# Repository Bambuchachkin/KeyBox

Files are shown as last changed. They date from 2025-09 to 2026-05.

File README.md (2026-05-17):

# KeyBox 🔑

(*Для того чтобы принять участие в обсуждении проекта можете перейти по ссылке https://github.com/Bambuchachkin/KeyBox/discussions/1)

## Цель проекта 🎯
Создать устройство, предназначенное для одновременного хранения ~ 10 ключей от
аудиторий в корпусах МФТИ. Оснастить его системой автоматического контроля
доступа к ключам через карты-пропуска. Вести учёт пользователей и времени, которое
ключи были у них на руках.

## Итоги работы ✨

### По итогам работы нашей команде удалось выполнить все поставленные цели:
1. ✅ Создано устройство для хранения 10 ключей
2. ✅ Установлен замок для ограничения доступа к ключам
3. ✅ Инсталирована светодиодная лента для улучшения пользовательского опыта
4. ✅ Реализована работа с картами-пропусками
5. ✅ Спроектирована база данных пользователей
6. ✅ Налажена работа с таблицами формата .xlsx для удобства работы с устройством
7. ✅ Разработаны методы работы с устройством с помощью консоли
8. ✅ Разработано и произведено функциональное устройство

<p align="center">
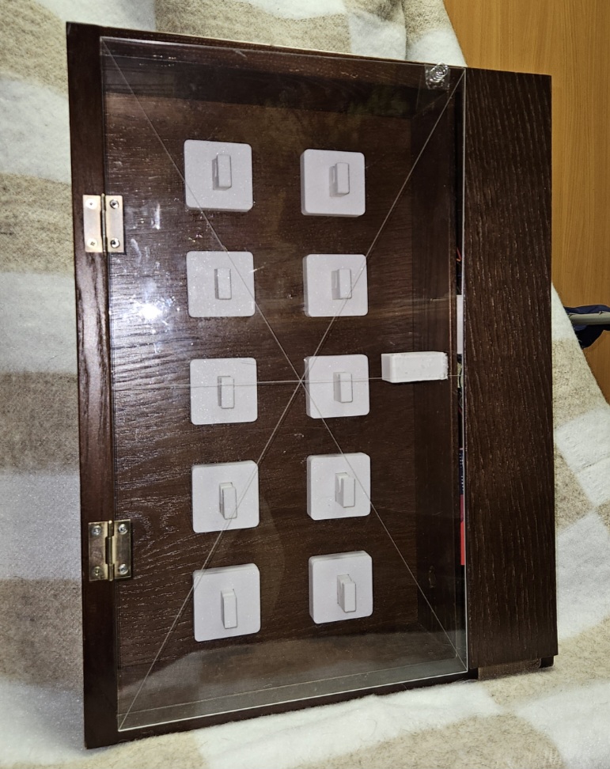
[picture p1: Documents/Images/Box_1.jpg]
  
</p>
<p align="center">
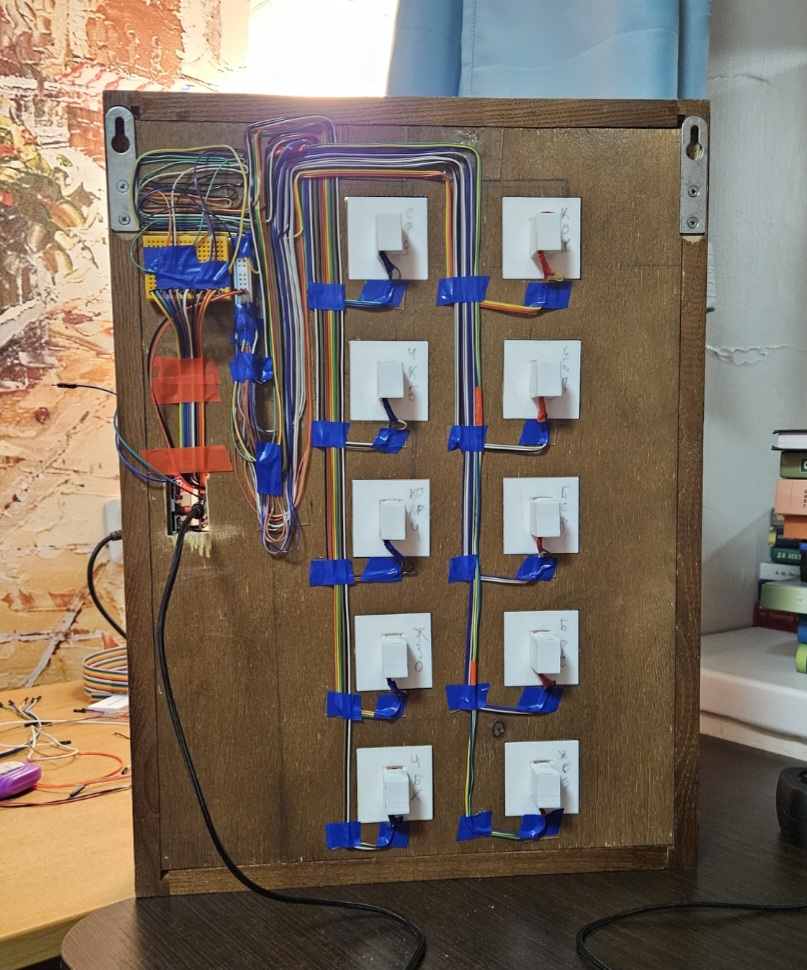
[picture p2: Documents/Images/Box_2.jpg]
  
</p>

### Решенные проблемы: 🔧
В процессе работы возникали проблемы различного уровня сложности. Среди наиболее острых, но разрешенных оказались:
1. Механизм открытия и закрытия двери, требующий от пользователя минимум действий, а именно приложить карту-пропуск и захлопнуть дверцу после взятия/возвращения ключа. Механизм был реализован при помощи системы: сервопривод, штифты и клинья, возвратные пружины.
2. Реализация наиболее удобных способов взаимодействия персонала с устройством. Такими являются консольное взаимодействие для быстрой регистрации и редактирования профилей пользователей и exel-таблицы для обработки базы данных и журнальных записей (приходы, уходы, взятые ключи).

### Возможное развитие проекта: 🚀
Полученное изделие имеет массу возможностей для улучшения:
1. Дистанционное взаимодействие посредством сети wi-fi
2. Оповещающие устройства (сигнальный динамик, информирующий дисплей)
3. Система автономного реагирования (автоматические ограничения для недобросовестных пользователей)

## Далее вы можете более подробно ознакомиться с историей развития проекта 📖

### Принципиальная схема цепи и взаимодействия ее компонент:

<p align="center">
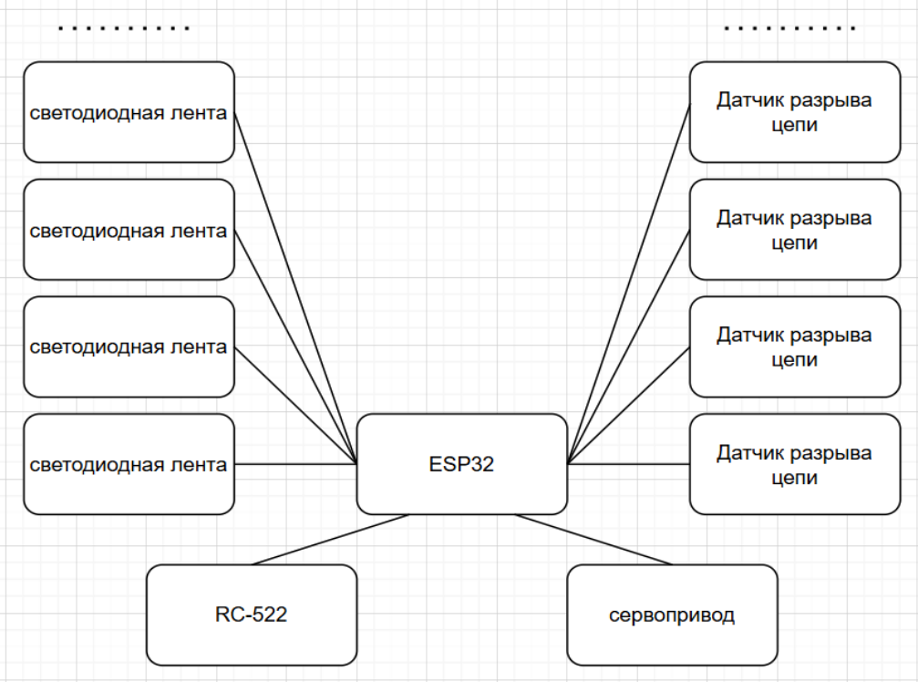
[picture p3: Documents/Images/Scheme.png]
  
</p>
<p align="center">
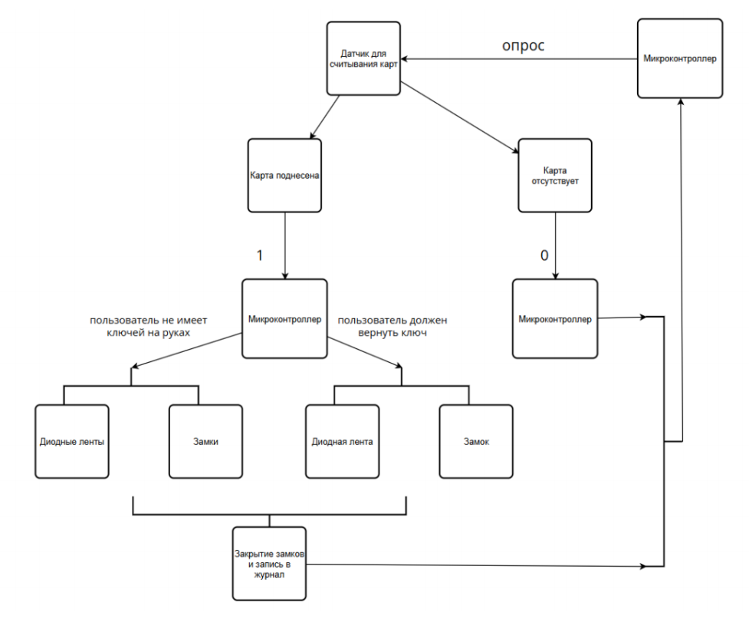
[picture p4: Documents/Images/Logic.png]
  
</p>

## Ход работы

### Особенности физтеховских карт-пропусков:
<table>
<tr>
<td style="border: none;">

Наименование: mifare classic 1k

Рабочая частота: 13.56 МГц

Требует аутентификации: Для данных, но не для UID

</td> </tr> </table>

### Взаимодействие с картой:
Общение с картами будет осуществлятся при помощи считывателя RC522.
<p align="center">
  ESP32 Tetris Console
</p>
<p align="center">
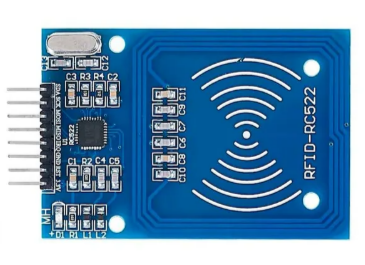
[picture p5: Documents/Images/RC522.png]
  
</p>
<!-- ![Отрисовка карты.](Documents/Images/RC522.png) -->

### Работа в материале

Схема работы детектирующего устройства:
<p align="center">
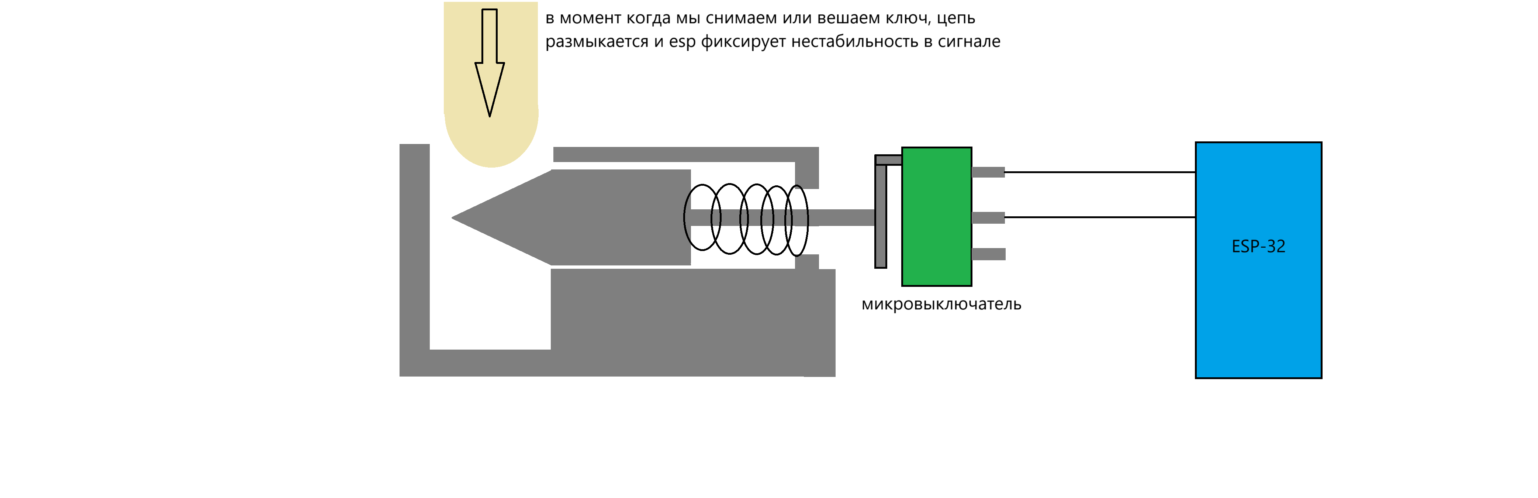
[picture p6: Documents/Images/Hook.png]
  
</p>

Модель корпуса ключницы:
<p align="center">
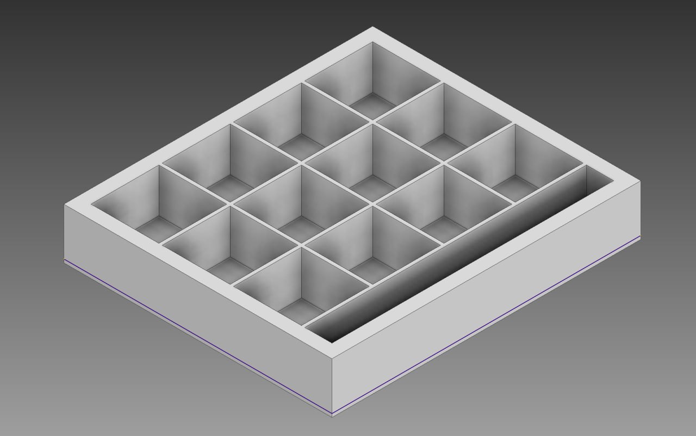
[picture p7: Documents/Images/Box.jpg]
  
</p>

Сделан корпус из дерева (дополнительные отверстия будут делаться на физтех-фабрике)
<p align="center">
  ESP32 Tetris Console
</p>
<!-- <img width="767" height="1207" alt="image" src="https://github.com/user-attachments/assets/810f8d19-dff7-42e2-9041-3b519ff64c55" /> -->
<!-- 
Реализация чтения данных пользователей из таблицы (предитоговая версия):
![Отрисовка карты.](Documents/Images/json_read.png) -->

### Написание кода
Реализация взаимодействия с RC522:
<p align="center">
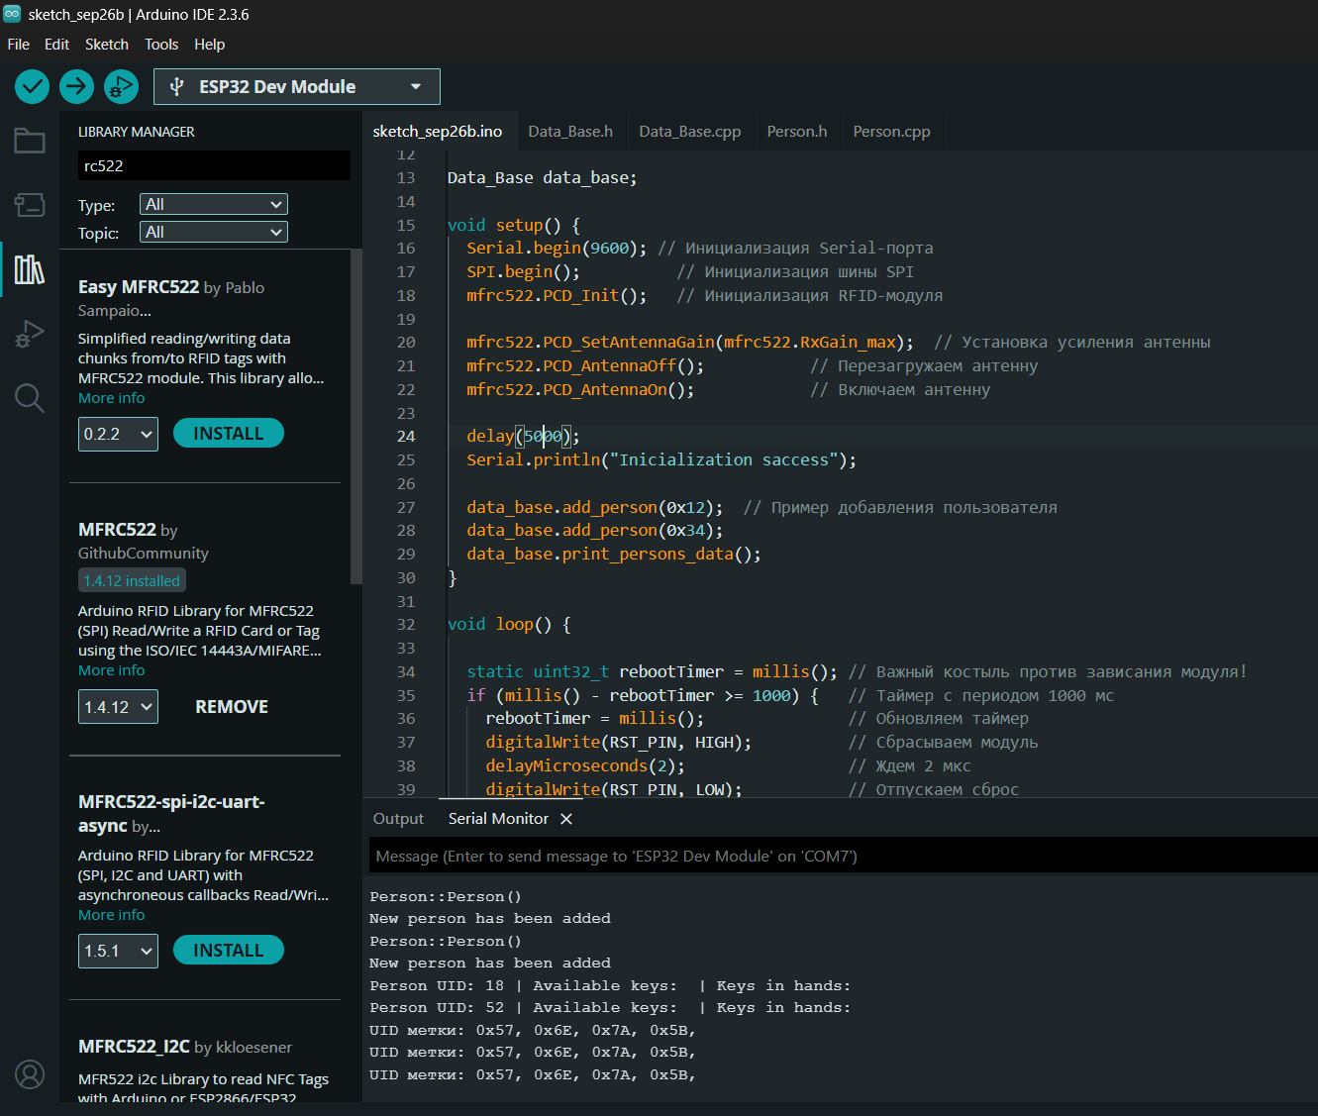
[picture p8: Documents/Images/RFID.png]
  
</p>

Реализация обработки команд с консоли:
<p align="center">
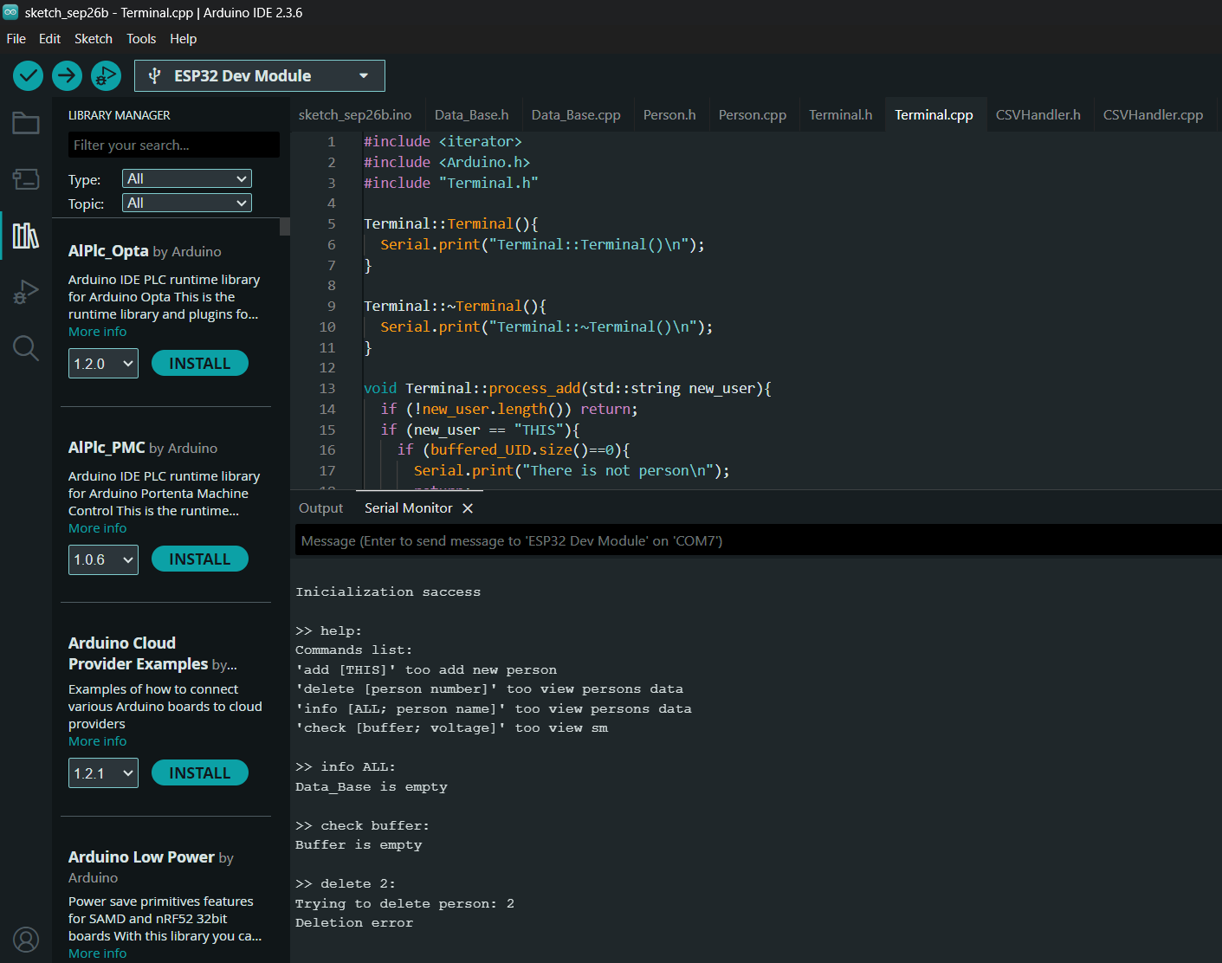
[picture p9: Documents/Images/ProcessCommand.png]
  
</p>

Реализация работы с пользователями:
<p align="center">
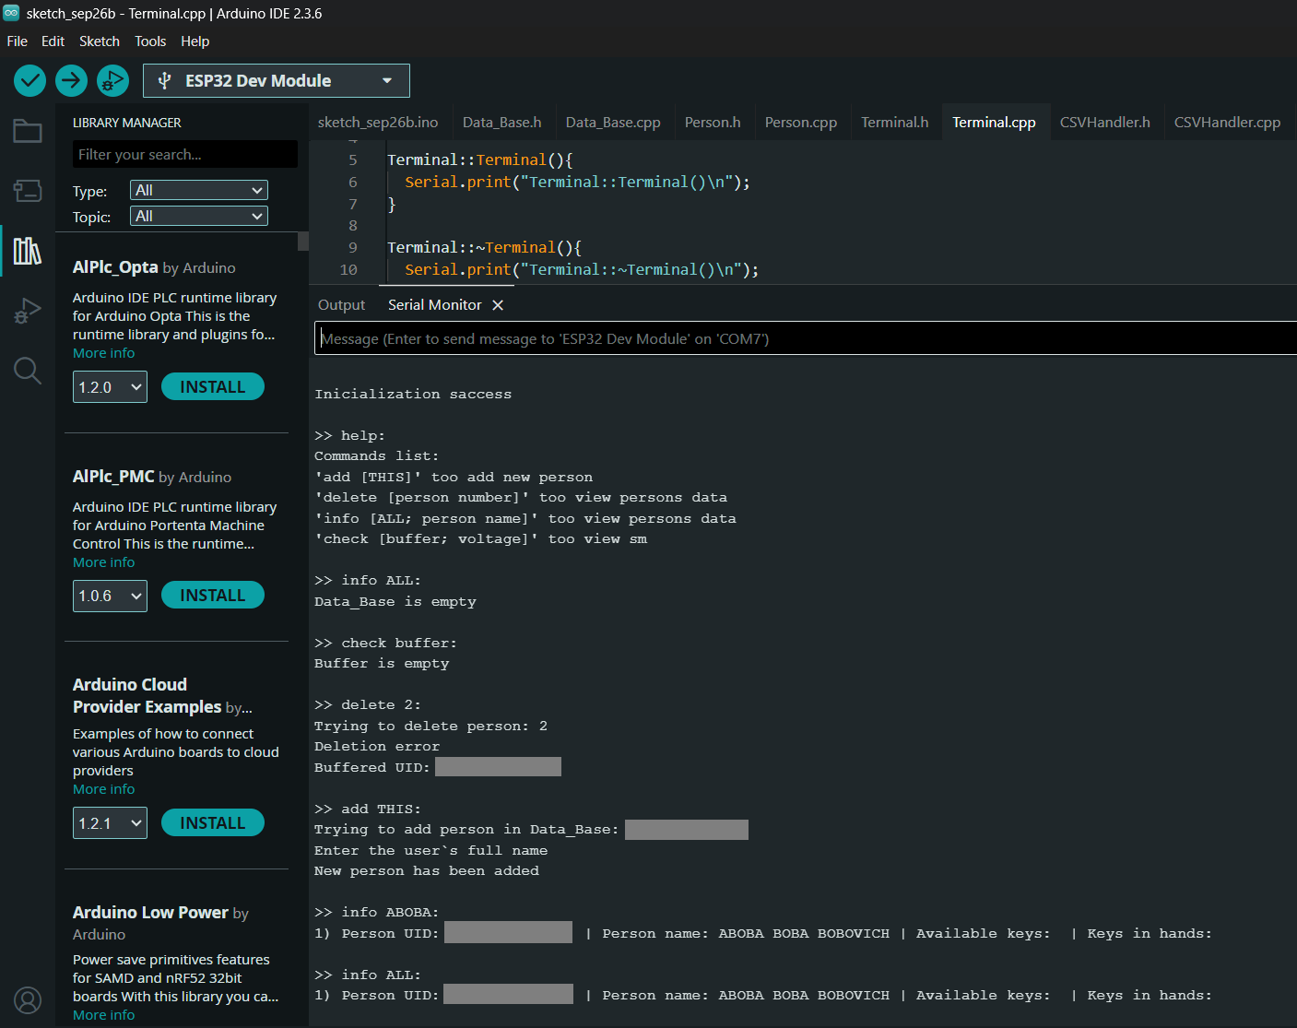
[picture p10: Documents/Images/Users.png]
  
</p>

Разработка структуры хранения данных:
<p align="center">
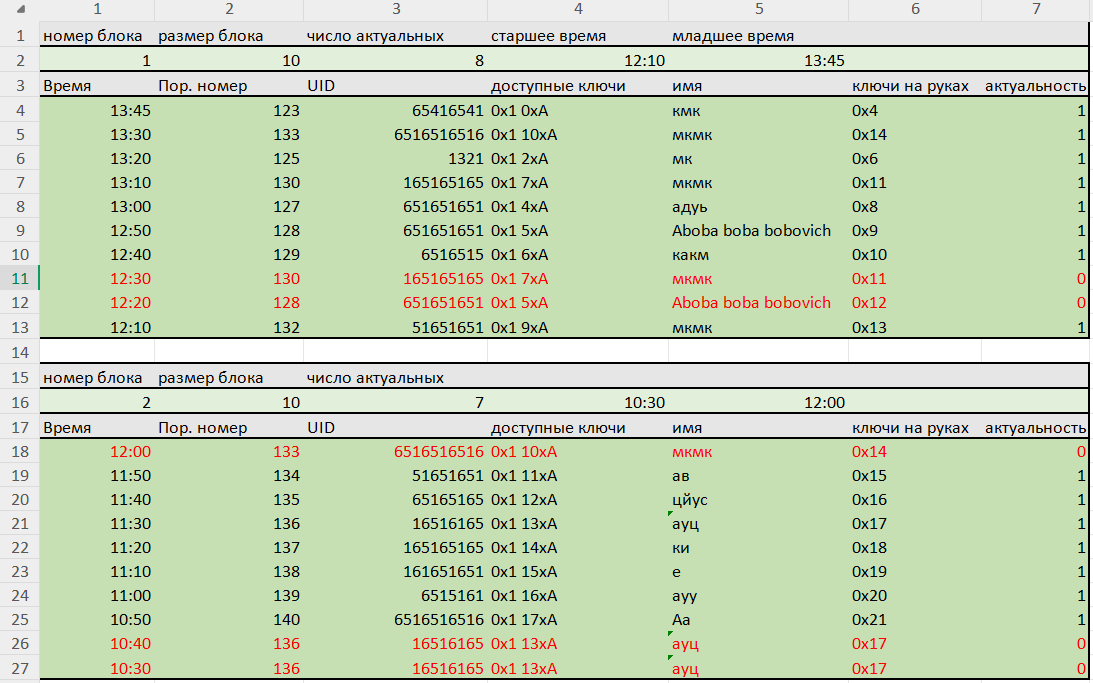
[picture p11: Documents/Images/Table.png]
  
</p>

Реализация чтения и записи данных в таблицу (тестовые отправки):
<p align="center">
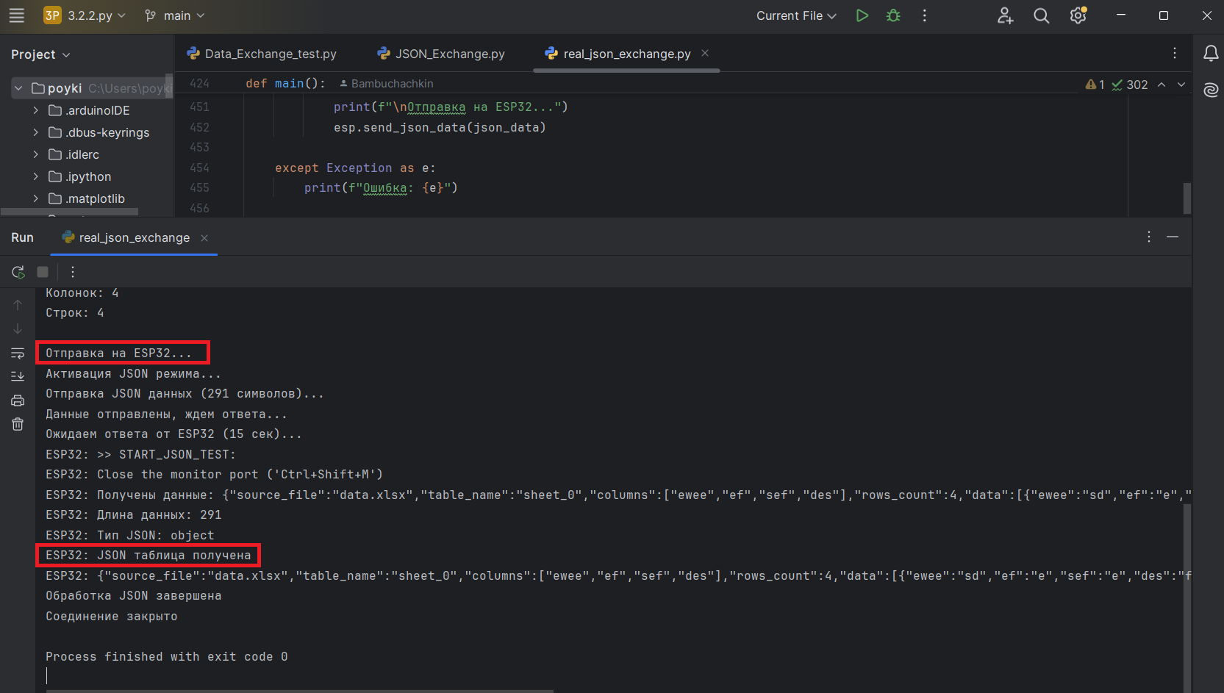
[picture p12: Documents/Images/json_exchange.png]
  
</p>

Реализация хранения и восстановления данных из постоянной памяти:
<p align="center">
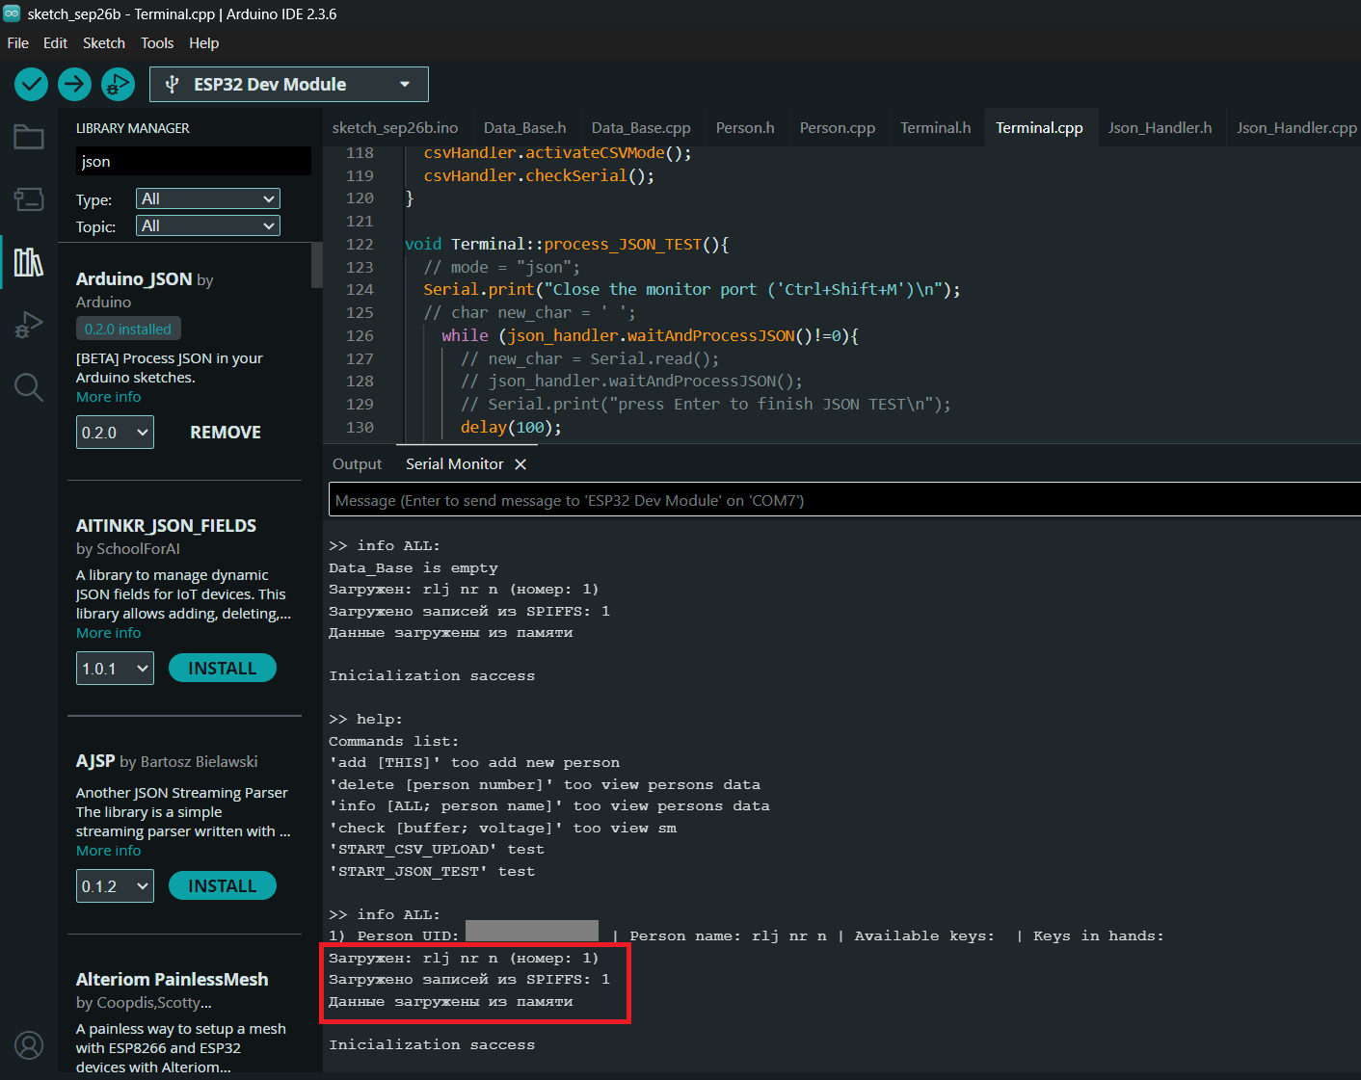
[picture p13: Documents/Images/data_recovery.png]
  
</p>

<!-- Добавлен кармашек для  зажима микропереключателя:
<img width="1541" height="1035" alt="image" src="https://github.com/user-attachments/assets/2c278192-2b9a-40d1-a9de-ddc6e570d0b0" />

Доработана основная платформа для закрепления кармашка в ней, так же увеличен радиус отерстия для пружинки:
<img width="1212" height="1104" alt="image" src="https://github.com/user-attachments/assets/5a2353b9-1f5b-4b1b-9aa3-503ce4ea96b2" /> -->

Окончательная реализация чтения данных пользователей из таблицы:
<p align="center">
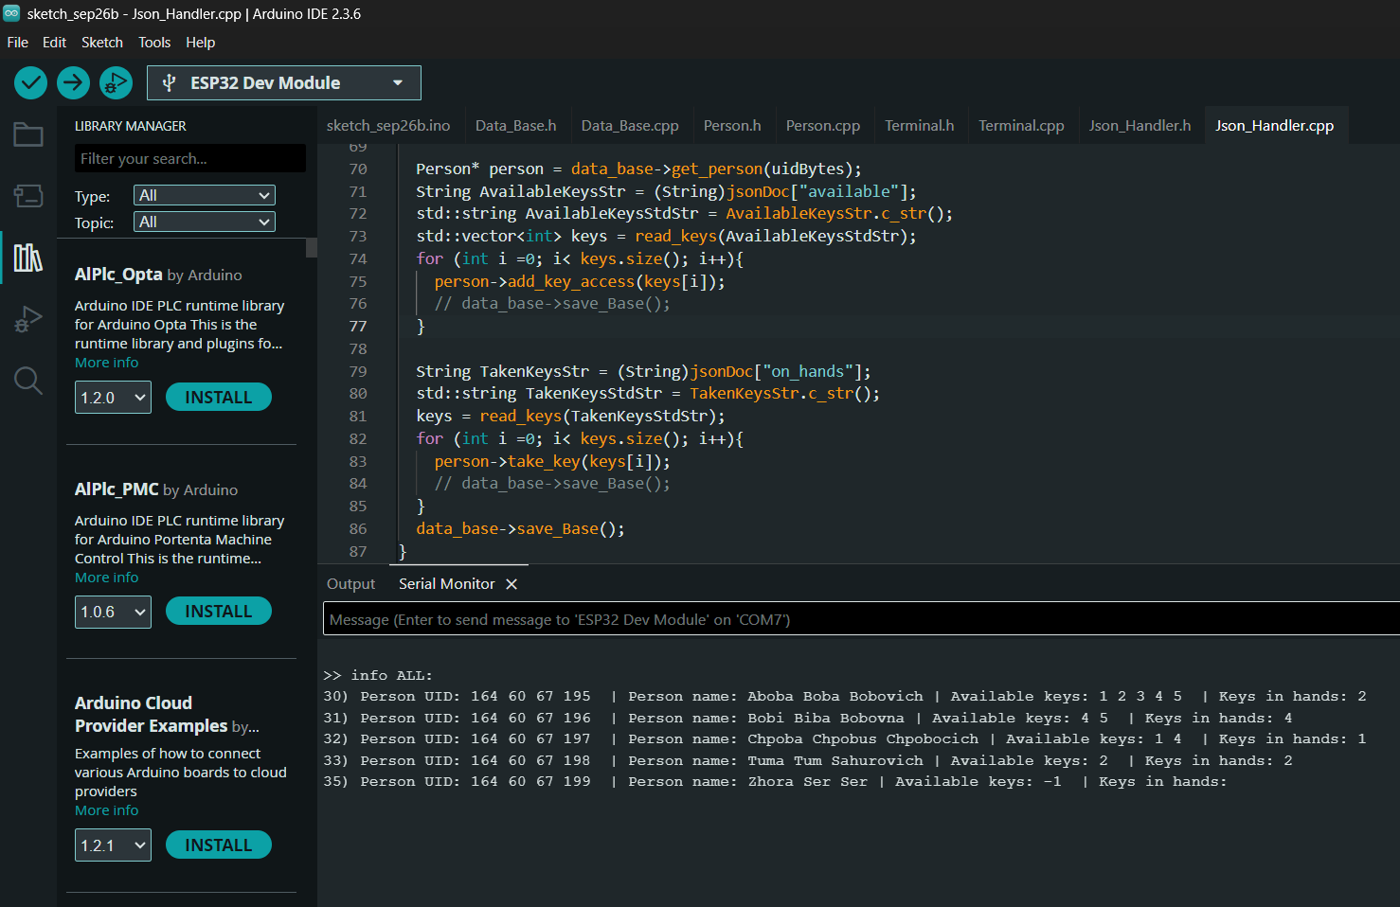
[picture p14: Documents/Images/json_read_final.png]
  
</p>

Сборка и тестирование 2ух узлов схемы + отладка кода:
<p align="center">
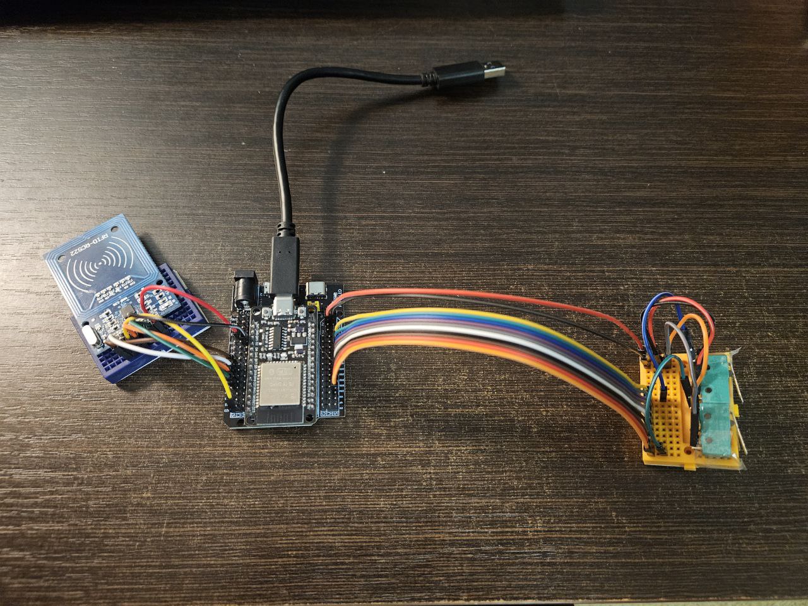
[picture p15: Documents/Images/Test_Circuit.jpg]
  
</p>

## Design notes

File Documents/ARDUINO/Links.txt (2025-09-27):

https://github.com/ljos/MFRC522/blob/master/MFRC522.h

https://alexgyver.ru/arduino-rfid/

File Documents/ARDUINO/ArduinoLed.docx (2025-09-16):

Основа всего проекта – это Arduino. Будем использовать Arduino Uno R3.

Необходимые о ней данные:

Характеристики Arduino UNO R3:

- Напряжение питания: 5 В
- Входное напряжение (рекомендуемое): 7-12 В
- Входное напряжение (предельное): 6-20 В
- Цифровой ввод-вывод: 14 линий (6 из них - ШИМ)
- Аналоговые входы: 6
- Постоянный ток на линиях ввода-вывода: 40 мА
- Постоянный ток на линии 3.3В: 50 мА
- Flash-память: 32 кб, 0.5 кб из них используются для загрузчика
- SRAM-память: 2 кб
- EEPROM-память: 1 кб
- Тактовая частота: 16 МГц

Для работы с подсветкой подойдет к примеру такая лента:

# https://giant4.ru/catalog/spi-lenta/ws2812b-60-ip33/? WS2812B 60 led

Или такая: https://www.ozon.ru/product/adresnaya-lenta-ws2812b-60-led-ip67-2-m-2210055581/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 (https://www.ozon.ru/product/adresnaya-lenta-ws2812b-60-led-ip67-2-m-2210055581/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) (идентичная)

Теперь по подключению:
1. Ограничение по Arduino Uno:

- Arduino Uno управляет лентой только по одному цифровому пину.
- Управление можно вести хоть 1000 светодиодов — ограничение в оперативной памяти (2 КБ).
- На каждый диод нужно 3 байта (RGB). 2000 байт ÷ 3, получается где-то около 600 светодиодов максимум.
- В этом случае дофига короче выйдет

Питание: ограничение только блоком питания. (Все зависит от него!!!!) От самой ардуинки лучше не питать более 10 диодов.

https://xn--18-6kcdusowgbt1a4b.xn--p1ai/ws2812b-%D0%B0%D1%80%D0%B4%D1%83%D0%B8%D0%BD%D0%BE/ (https://xn--18-6kcdusowgbt1a4b.xn--p1ai/ws2812b-%D0%B0%D1%80%D0%B4%D1%83%D0%B8%D0%BD%D0%BE/) - здесь хорошо описано подключение нашей ленты (если надо выведу информацию в README)

+5В блока питания ---- +5В ленты

GND блока питания ---- GND ленты

+--- GND Arduino

DIN ленты ----------- Цифровой пин Arduino (например, D6 через резистор 330 Ом) – это в слусае наличия блока питания ( повербанк)

Под конец)) Советы от гпт (думаю что правильные)

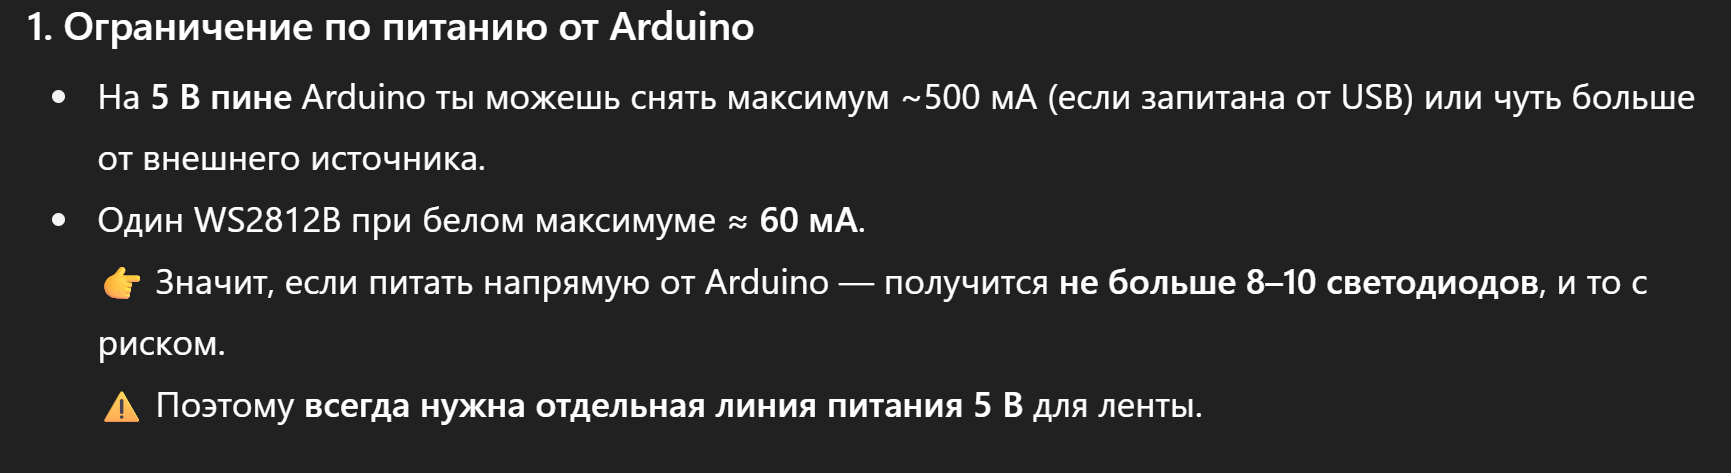
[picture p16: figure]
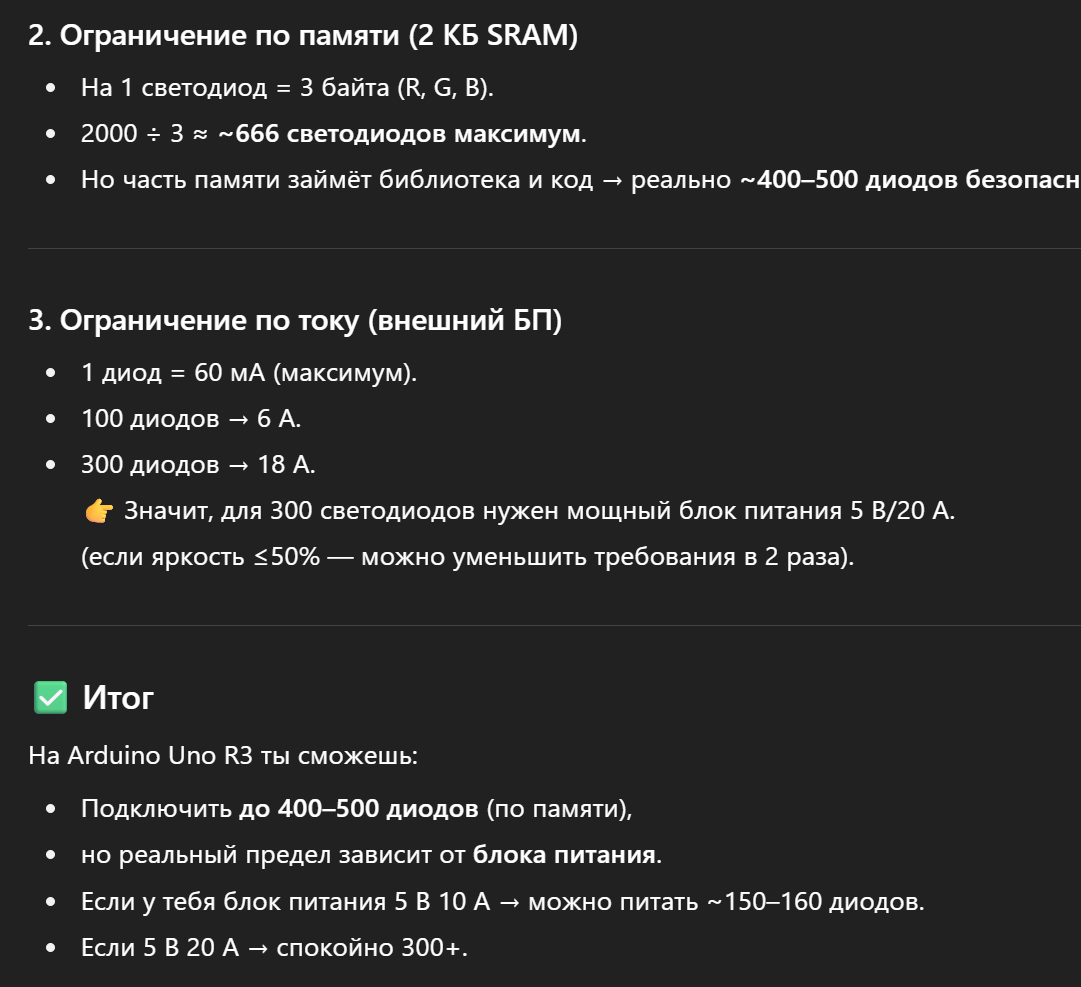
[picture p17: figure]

Тип | Обозначение на плате | Номер вывода MCU | Полное название/Расшифровка | Функция и назначение
Цифровые | 0 | PD0 | RX (Receive) | Приём данных по UART (последовательный порт). Также используется для загрузки скетчей. Не используйте, если подключен USB.
| 1 | PD1 | TX (Transmit) | Передача данных по UART. Аналогично, не используйте при активном USB-соединении.
| 2 | PD2 | INT0 (External Interrupt 0) | Цифровой ввод/вывод. Внешнее прерывание 0.
| 3 | PD3 | INT1 (External Interrupt 1) / PWM | Цифровой ввод/вывод. Внешнее прерывание 1. ШИМ (PWM) вывод.
| 4 | PD4 | | Цифровой ввод/вывод.
| 5 | PD5 | PWM | Цифровой ввод/вывод. ШИМ (PWM) вывод.
| 6 | PD6 | PWM | Цифровой ввод/вывод. ШИМ (PWM) вывод.
| 7 | PD7 | | Цифровой ввод/вывод.
| 8 | PB0 | | Цифровой ввод/вывод.
| 9 | PB1 | PWM | Цифровой ввод/вывод. ШИМ (PWM) вывод.
| 10 | PB2 | PWM / SS (Slave Select) | Цифровой ввод/вывод. ШИМ (PWM) вывод. Выбор ведомого устройства (SS) для SPI.
| 11 | PB3 | PWM / MOSI (Master Out Slave In) | Цифровой ввод/вывод. ШИМ (PWM) вывод. Линия данных MOSI для SPI.
| 12 | PB4 | MISO (Master In Slave Out) | Цифровой ввод/вывод. Линия данных MISO для SPI.
| 13 | PB5 | SCK (Serial Clock) | Цифровой ввод/вывод. Тактовый сигнал (SCK) для SPI. К этому пину подключен светодиод L.
Аналоговые | A0 | PC0 | | Аналоговый вход №0. Также может быть цифровым вводом/выводом.
| A1 | PC1 | | Аналоговый вход №1. Также может быть цифровым вводом/выводом.
| A2 | PC2 | | Аналоговый вход №2. Также может быть цифровым вводом/выводом.
| A3 | PC3 | | Аналоговый вход №3. Также может быть цифровым вводом/выводом.
| A4 | PC4 | SDA (Serial Data) | Аналоговый вход №4. Также может быть цифровым вводом/выводом. Линия данных SDA для интерфейса I²C (TWI).
| A5 | PC5 | SCL (Serial Clock) | Аналоговый вход №5. Также может быть цифровым вводом/выводом. Линия тактирования SCL для интерфейса I²C (TWI).
Питание | VIN | | Voltage Input | 1) Вход: Напряжение от внешнего источника (через разъем Jack). 2) Выход: Если плата питается от USB, здесь будет ~5V.
| 5V | | +5 Volts | Выход стабилизированного напряжения +5V от платного стабилизатора. Для питания модулей.
| 3.3V | | +3.3 Volts | Выход стабилизированного напряжения +3.3V. Мощность ограничена (~50 мА).
| GND | | Ground | Земля (общий провод). На плате несколько таких контактов.
| RESET | PC6 | Reset | Вход. Подача низкого уровня (LOW) на этот пин вызывает перезагрузку процессора.
| AREF | | Analog Reference | Вход для опорного напряжения для аналоговых входов (A0-A5). По умолчанию опорное — 5V.
Спец. разъёмы | ICSP (для MCU) | | In-Circuit Serial Programming | 6-пиновый разъём для прямого программирования микроконтроллера ATmega328P в обход загрузчика. Дублирует пины SPI: MISO, MOSI, SCK, RESET, VCC, GND.
| ICSP (для USB-чипа) | | In-Circuit Serial Programming | 6-пиновый разъём для программирования микроконтроллера ATmega16U2 (отвечает за USB).
| USB | | Universal Serial Bus | Порт USB Type-B. Для питания, программирования и последовательной связи (UART) с компьютером.
| POWER | | DC Barrel Jack | Вход для внешнего источника питания 7-12V DC. Центральный контакт — плюс.

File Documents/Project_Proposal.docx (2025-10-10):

Практикум цифрового производства. Осень 2025

Предложение проекта: Автономный шкаф-ключница, с функцией ведения учёта пользователей.

Команда:

Пойкин Иван Дмитриевич Б01-401 poikin.id@phystech.edu

Кузнецов Матвей Юрьевич Б03-403 kuznetsov.miu@phystech.edu

Цель проекта:

Создать устройство, предназначенное для одновременного хранения ~ 10 ключей от аудиторий в корпусах МФТИ. Оснастить его системой автоматического контроля доступа к ключам через карты-пропуска. Вести учёт пользователей и времени, которое ключи были у них на руках.

Описание функционала:

1. ~ 10 отделений для хранения ключей, оснащённых замками для контроля доступа
2. Управляющая система на базе Arduino
3. Идентификация пользователя по карте-пропуску
4. Список доступных ключей, зависящий от прав пользователя
5. Учёт времени пользования ключом

Задачи проекта:

1. Изучить работу карт-пропусков
2. Произвести окончательный выбор платы Arduino
3. Разработать электрическую схему и закупить её составляющие
4. Разработать программный код для системы
5. Сконструировать шкаф-ключницу (создать необходимые чертежи и 3d-модели)
6. Произвести спроектированные детали
7. Собрать готовое изделие

Существующие аналоги:

Коммерческие решения:

1. KMS-20 - автоматическая ключница (https://logard.su/catalog/metallicheskaya-mebel/avtomaticheskie-klyuchnicy/kms-20-avtomaticheskaya-klyuchnica/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)

Преимущества: Российское производство, прочность материалов, возможность интеграции с другими системами безопасности, идентификация по карте-пропуску.

Недостатки: высокая цена ~ 250 тыс. руб., излишняя защищённость в нашей ситуации.

2. Умная ключница от Tuya Smart (https://market.yandex.ru/card/umnaya-elektronnaya-kodovaya-klyuchnitsa-mini-seyf-s-vozmozhnostyu-udalennogo-upravleniya-kodami-dostupa-v-keyboks-s-ttlocktuya-app/443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)

Преимущества: доступность, идентификация по карте.

Недостатки: единственное отделение для хранения ключей.

Самодельные решения:

К сожалению, готового изделия найти не удалось. Но существуют часто упоминаемые идеи реализации: использование RFID-меток (аналогично нашей идее), использование датчиков движения для активации подсветки в тёмном помещении.

Большинство предложений из интернета связаны с домашним использованием. Поэтому функционал несколько отличается от нашей задумки. Компании предпочитают готовые решения, а близким людям не нужны функции контроля доступа.

В нашем случае не требуется антивандальная защита, но контроль должен выполняться.

Эскиз проекта:

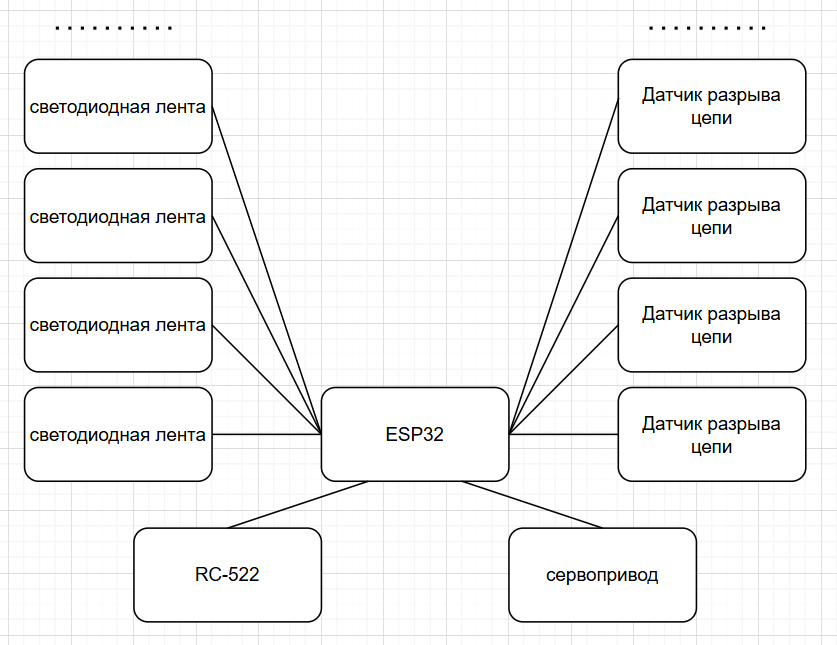
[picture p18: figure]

Логика работы:

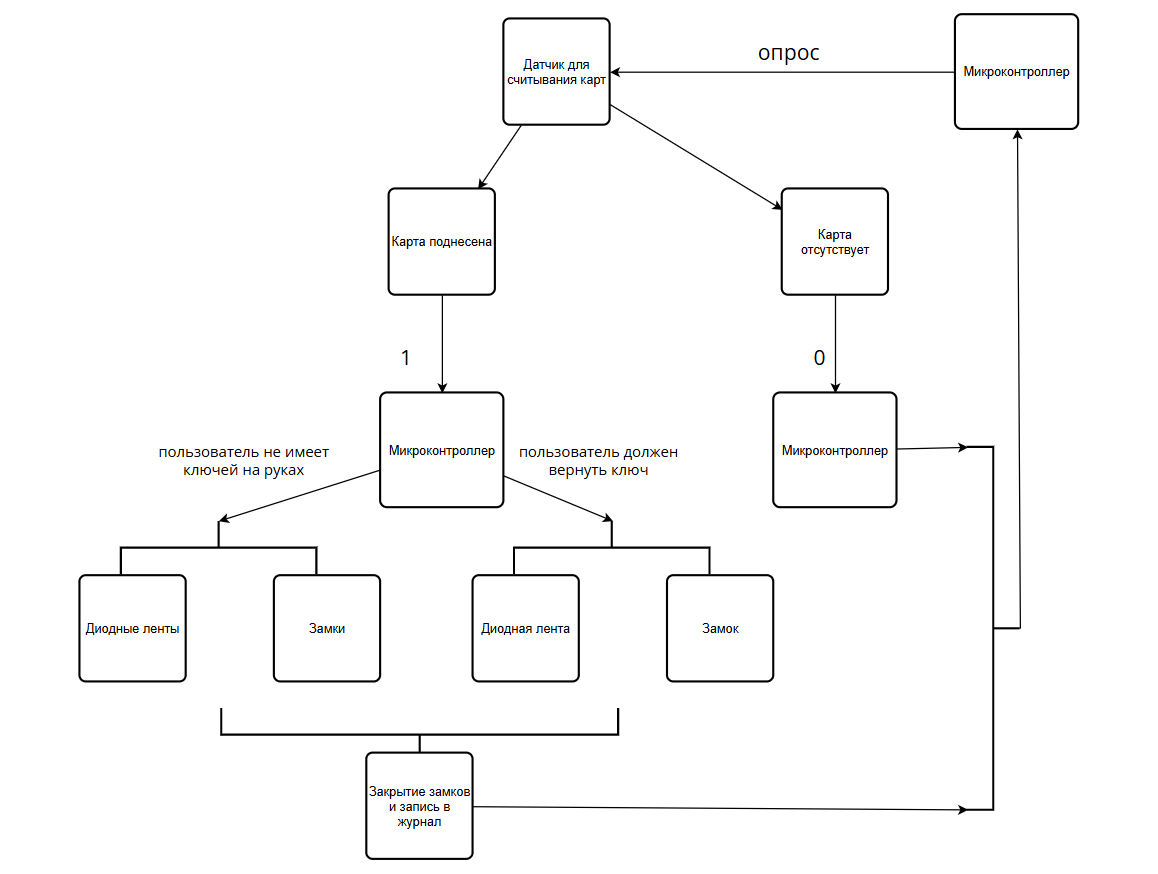
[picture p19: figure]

Элементная база:

1. Контроллер Arduino
2. Элементы питания цепи (портативный аккумулятор)
3. Светодиодные ленты (или другие индикаторы)
4. Устройство для считывания карт-пропусков
5. Замки для отсеков
6. Соединительные элементы цепи
7. Листы фанеры для изготовления корпуса
8. Крепёжные элементы корпуса

Используемое оборудование:

1. Любая доступная CAD-система
2. Станок для резки фанеры
3. 3D-принтеры

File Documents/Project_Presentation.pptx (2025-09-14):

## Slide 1

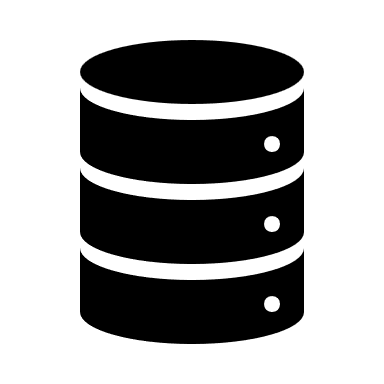
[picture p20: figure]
База данных со сплошной заливкой

Ключница

Подготовили: Кузнецов Матвей, Пойкин Иван

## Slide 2

Постановка задачи

Разработать устройство для хранения ключей от аудиторий и дополнить его системой для автоматизации выдачи ключей.

Цель

Ускорение и облегчегние процесса получения ключей

Автономная система учета

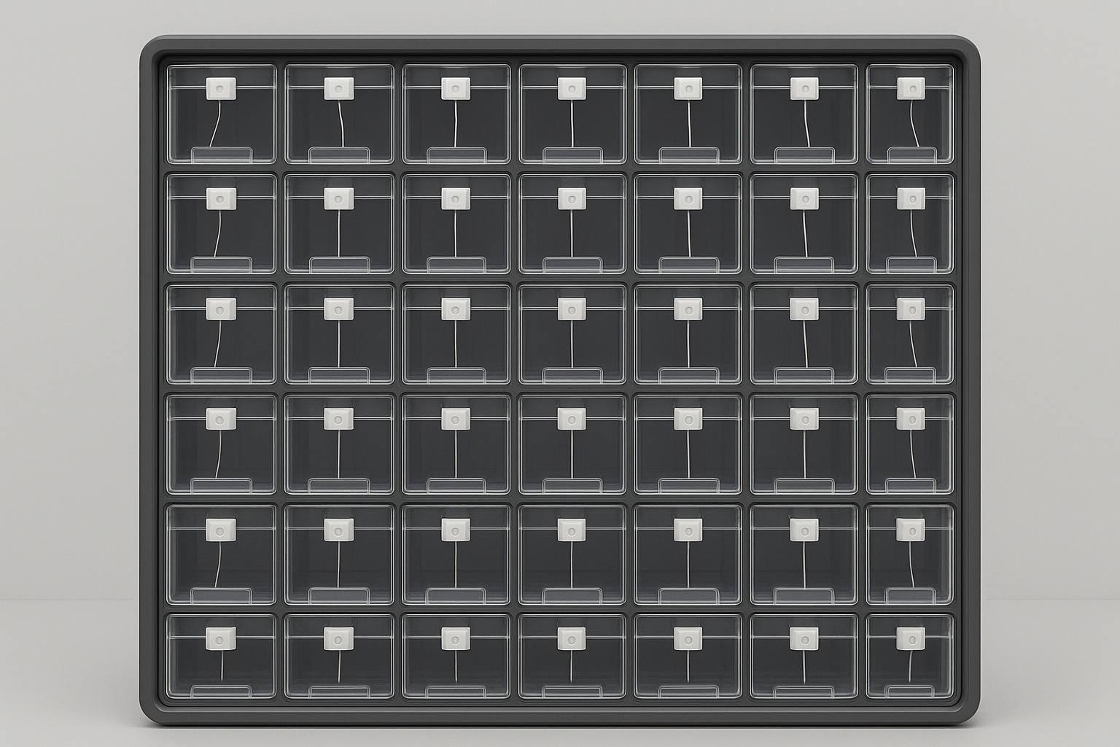
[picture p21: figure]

Облегченный поиск

Точечная подсветка указывает расположение

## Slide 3

Предполагаемый сценарий использования

Сотрудники корпусов вынуждены вести учет выдаваемых ключей. При этом записи вносятся на бумажный носитель, что увеличивает временные затраты.

Схема работы с ключницей

Пользователь прикладывает
карту-пропуск к аппарату

Система дает доступ
к разрешенным ключам

Система фиксирует
действия пользователя

Узкими местами в действующей схеме являются журнал учета и способ создания новых записей.

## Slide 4

Функционал

Внесенный в базу данных пользователь будет автоматически получать возможность брать доступные ему ключи, без постороннего вмешательства

Идентификация пользователя

1

Отсеки выделяются с помощью светодиодов, что исключает путаницу и помогает быстро найти нужный предмет.

Индикация отсеков

2

Система фиксирует отсутствие ключа и запускает таймер, по истичени которого подает тревожный сигнал.

Датчики

3

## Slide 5

Процессы создания

- Изучение работы с пропускными картами
- Закупка необходимого оборудования для работы с картами
- Разработка программного обеспечения ключницы
- Сборка корпуса и электрической цепи

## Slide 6

Необходимые компоненты и ресурсы Фабрики

- Фанера и элементы крепежа для корпуса
- Arduino
- Светодиодные ленты
- Элементы питания
- Остальные составляющие электрической цепи
- Лазерный станок для резки фанеры
- 3D-принтеры

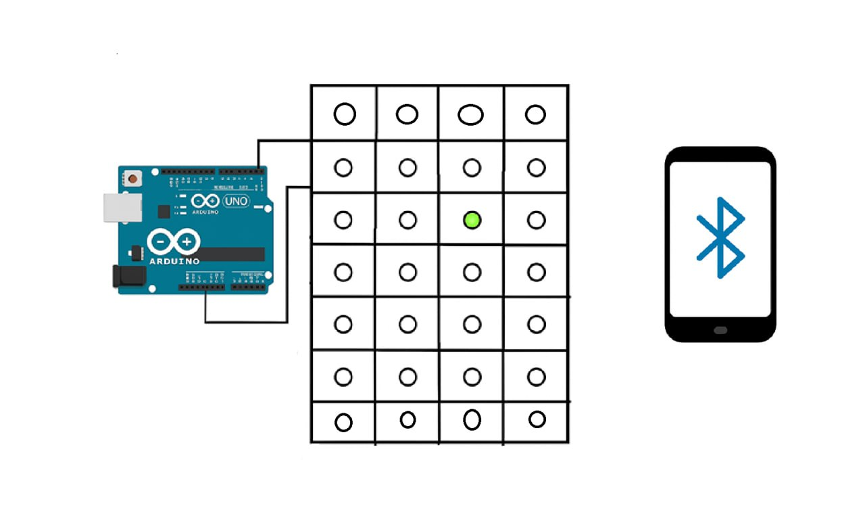
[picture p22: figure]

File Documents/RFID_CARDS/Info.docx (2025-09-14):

Виды RFID меток:

1. Низкочастотные 125 кГц
2. Высокочастотные 13,56 МГц

Физтеховская RFID карта пропуск:

mifare classic 1k - 13.56 МГц

Высокочастотные RFID метки (13.56 МГц):

Будем запрашивать uid карты. Занесем uid доверенных пользователей в базу. (Излишняя безопасность с использованием защищенных полей пока не нужна, тем более, что к ним у нас нет доступа. Их можно подключить в перспективе)

Именно это и есть наш вариант.

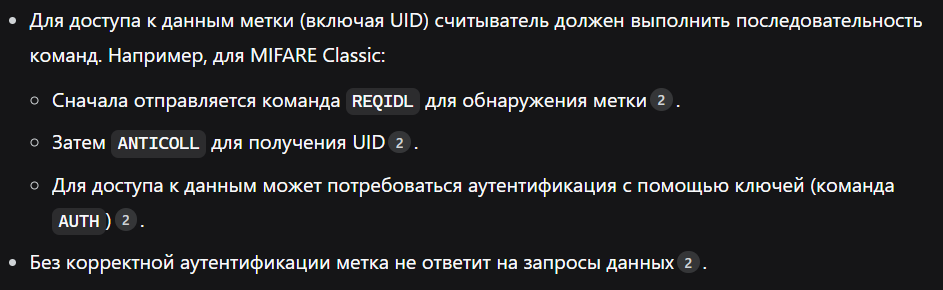
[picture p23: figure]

В таком случае будем работать пока с чистыми картами. В дальнейшем попробуем договориться с руководством. Иначе представим проект с незащищенными картами.

Тип метки | Частота | Автоматическая передача UID | Требует аутентификации | Примечания
MIFARE Classic 1K | HF (13.56 МГц) | Да (в протоколе) | Для данных, но не для UID | UID читается командой ANTICOLL

Но, все-таки, вроде бы, проблем быть не должно.

Предлагаю купить вот этот считыватель RC522 https://www.ozon.ru/product/rfid-modul-arduino-rc522-s-kartoy-i-brelokom-877579875/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

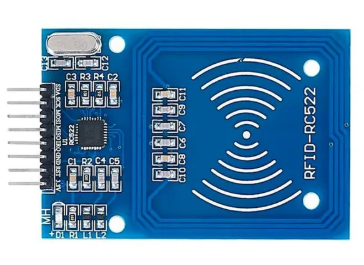
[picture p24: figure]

На него есть много гайдов и он очень дешевый.

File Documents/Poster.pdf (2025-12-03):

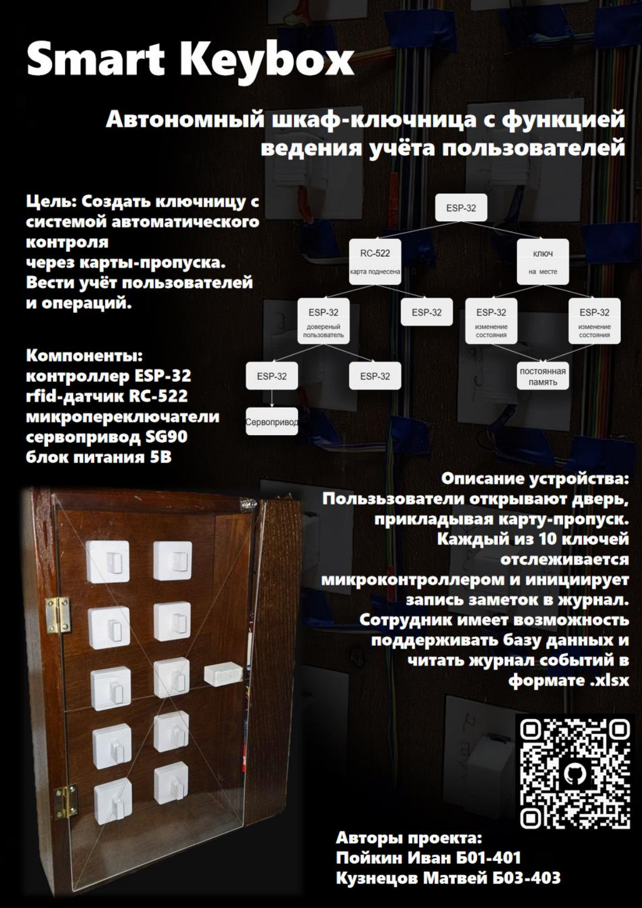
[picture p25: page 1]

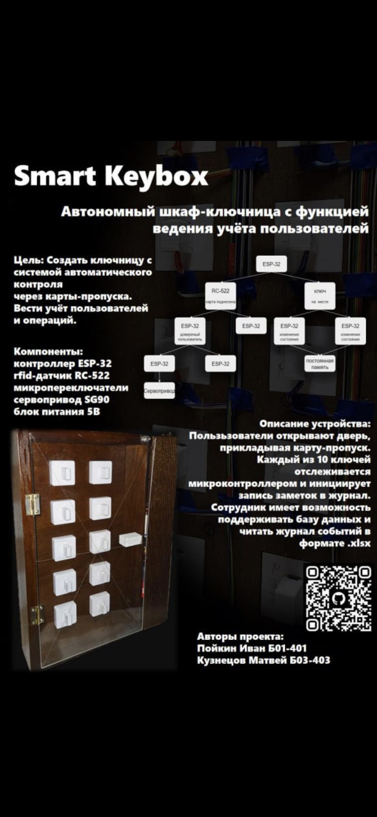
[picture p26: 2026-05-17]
Documents/Images/Poster.jpg

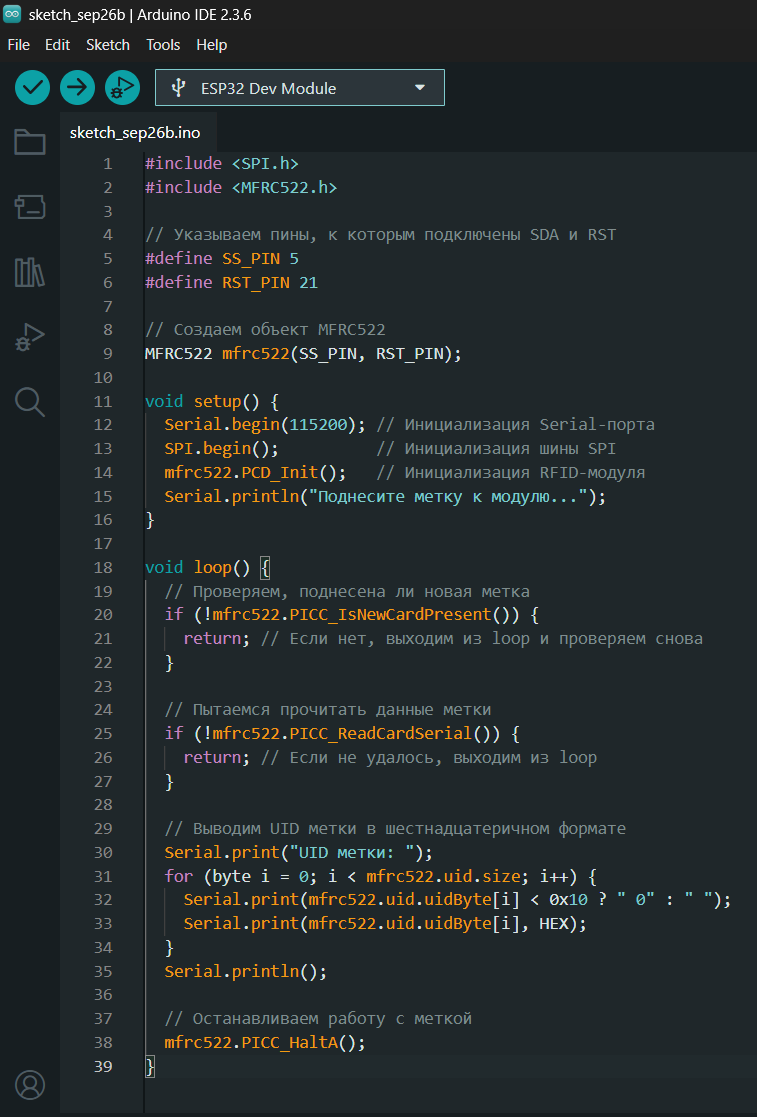
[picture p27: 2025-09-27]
Documents/Images/Sketch.png

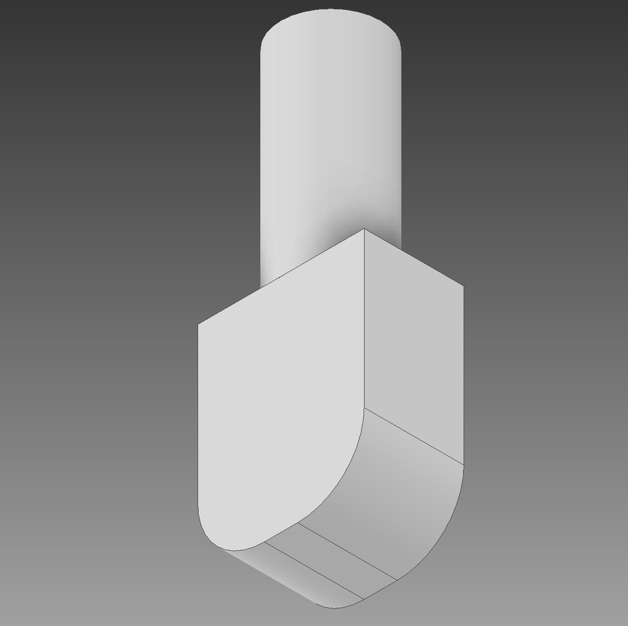
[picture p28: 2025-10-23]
Documents/Images/IceCream.jpg

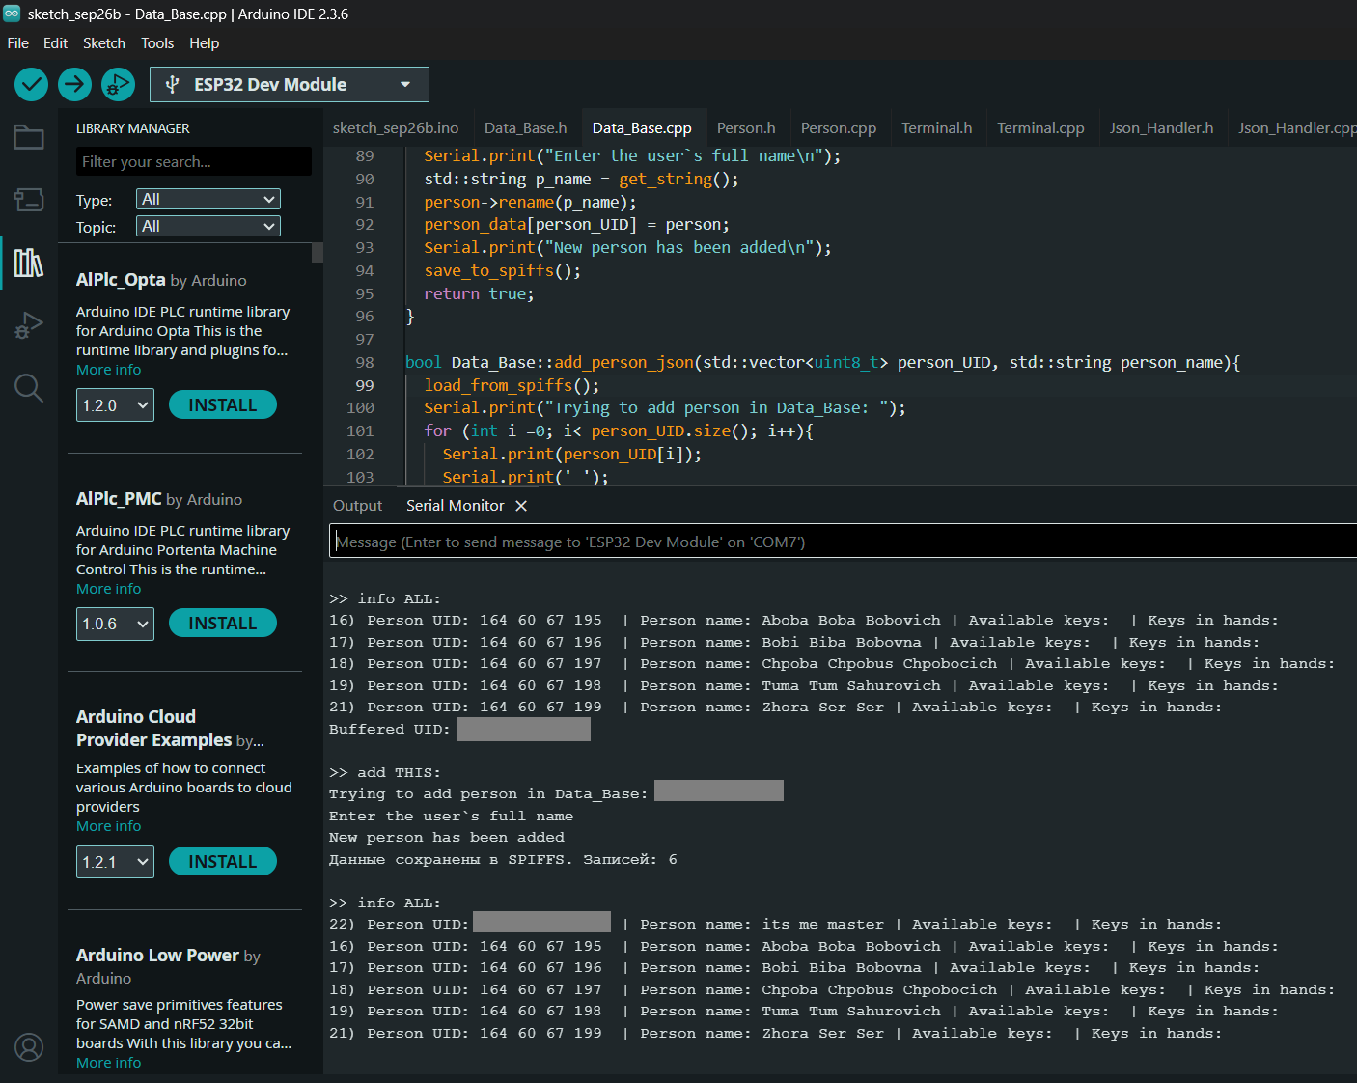
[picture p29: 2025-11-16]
Documents/Images/json_read.png

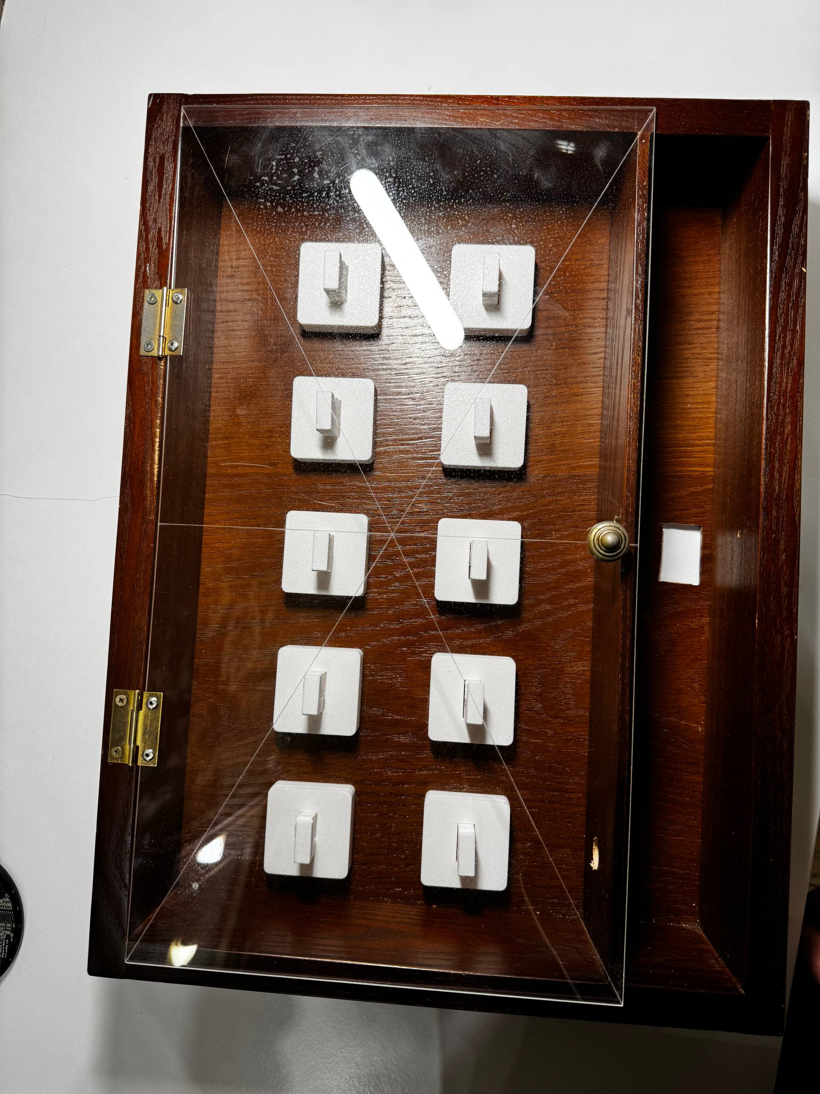
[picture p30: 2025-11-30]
Documents/Images/final_box.jpg

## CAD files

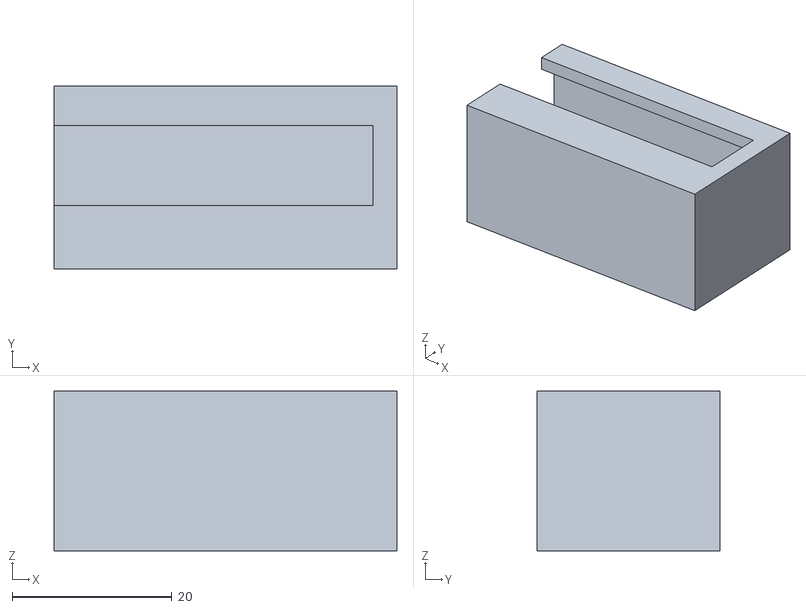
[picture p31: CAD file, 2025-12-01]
Components/rectandirka.stl
43.0 x 23.0 x 20.0

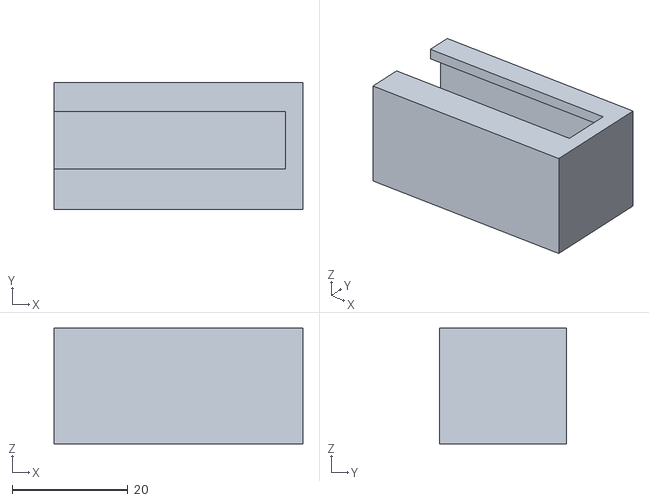
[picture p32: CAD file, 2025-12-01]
Components/rectandirka2.stl
43.0 x 22.0 x 20.0

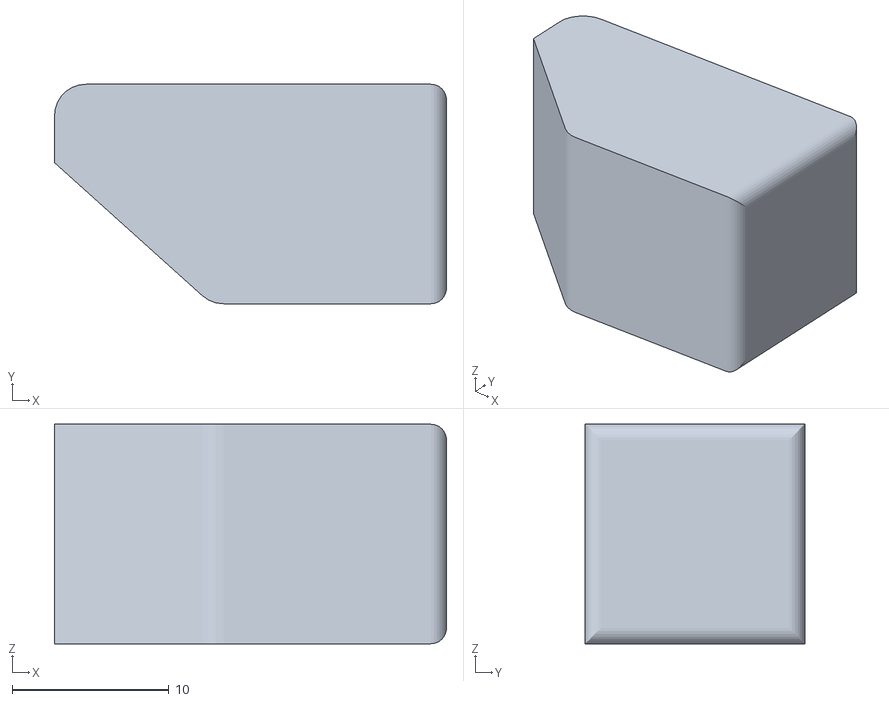
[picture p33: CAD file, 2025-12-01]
Components/prot2.stl
25.0 x 14.0 x 14.0

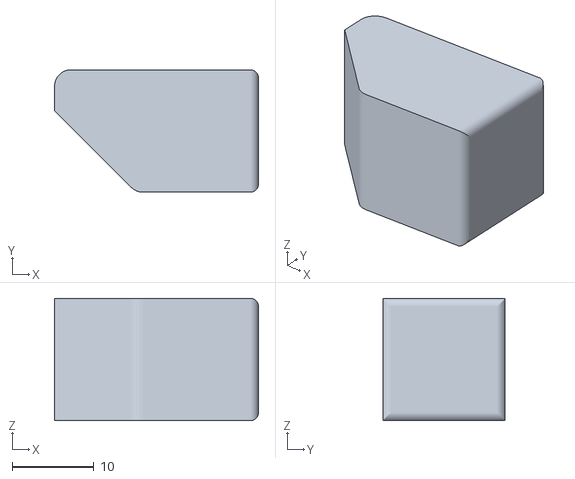
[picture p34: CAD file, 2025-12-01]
Components/prot1.stl
25.0 x 15.0 x 15.0

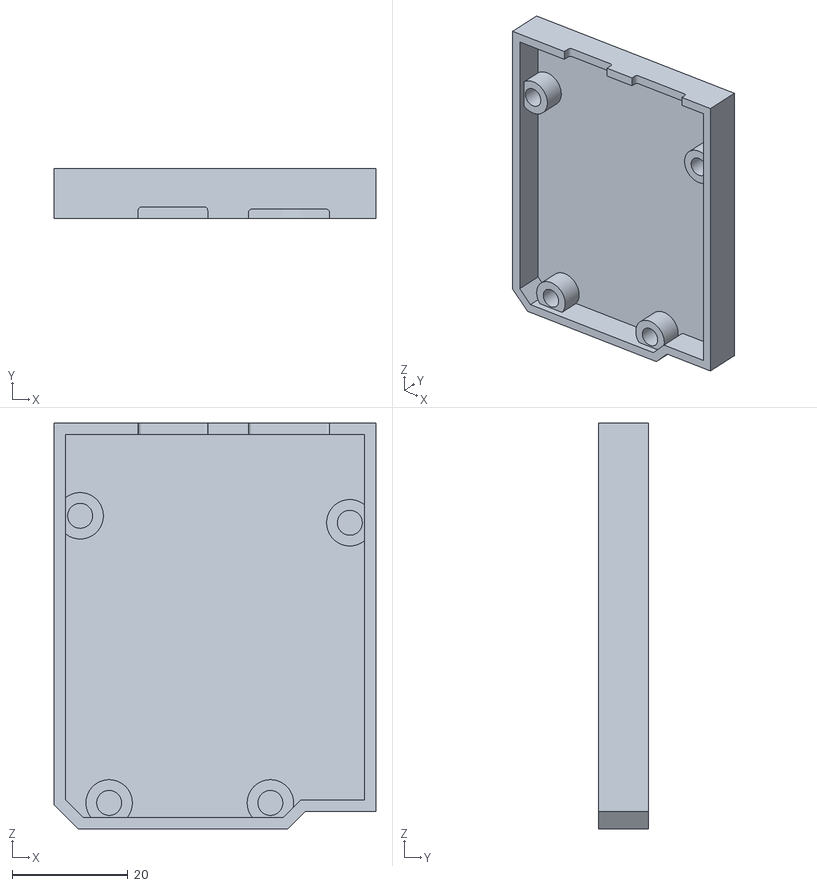
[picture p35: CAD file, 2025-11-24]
Components/baza.stl
55.5 x 8.60 x 70.0

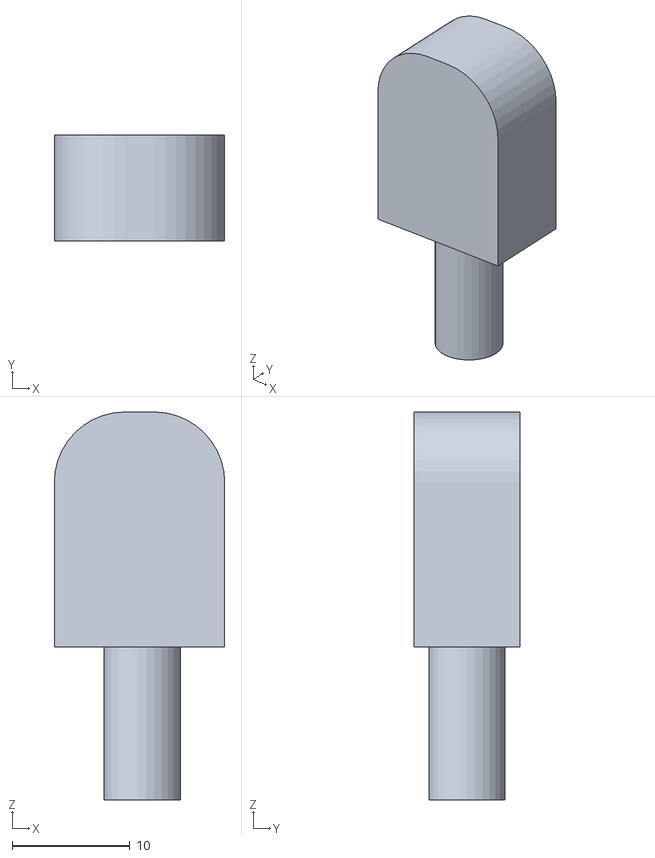
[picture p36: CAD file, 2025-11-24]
Components/moroshenka.stl
14.5 x 9.00 x 33.0

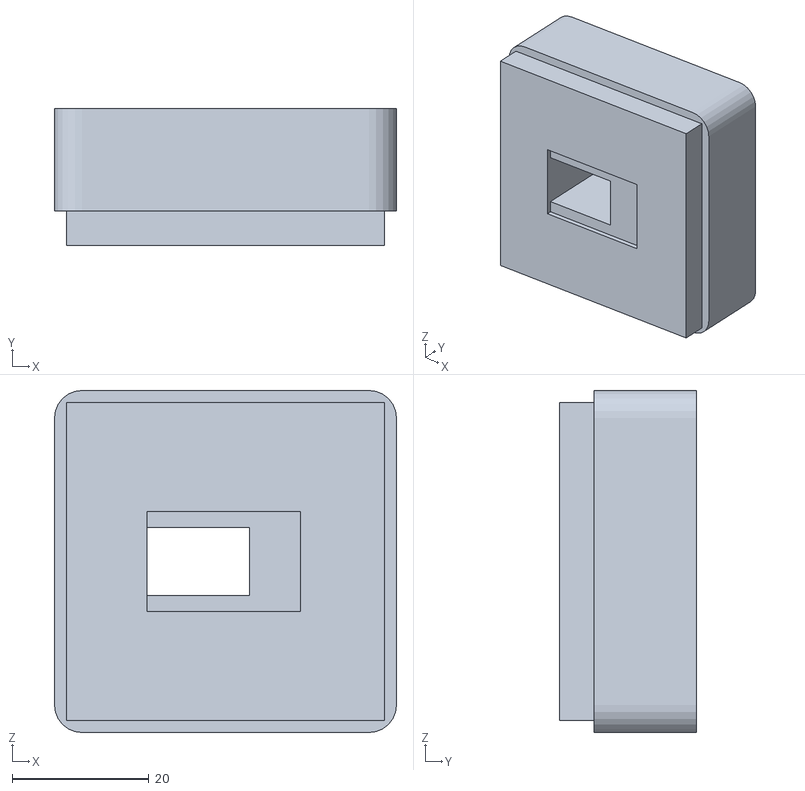
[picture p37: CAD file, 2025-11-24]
Components/platform.stl
50.0 x 20.0 x 50.0

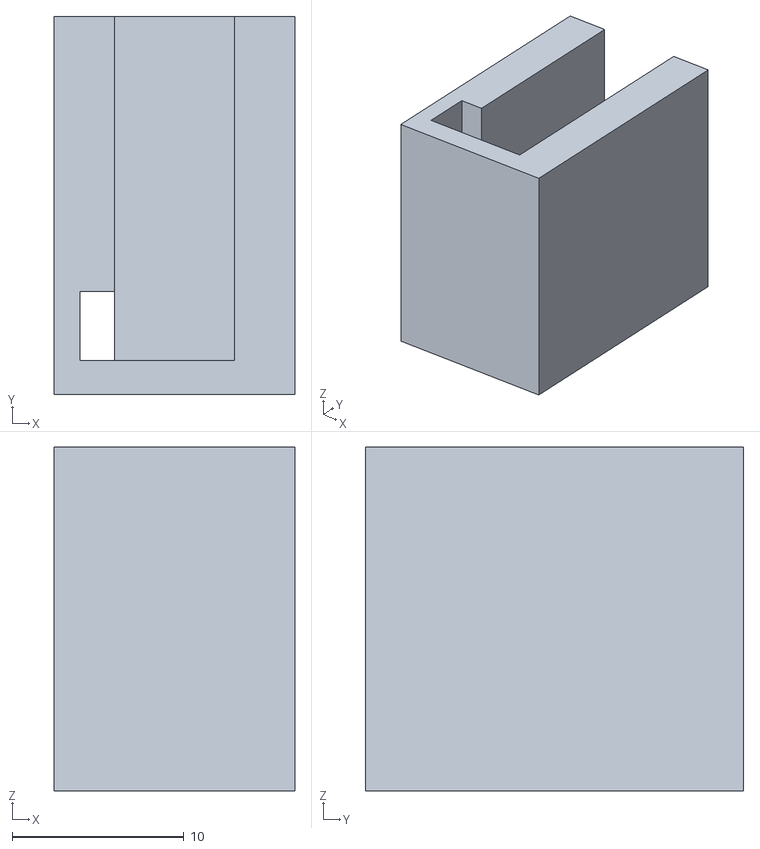
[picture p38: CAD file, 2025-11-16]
Components/karmashek.stl
14.0 x 22.0 x 20.0

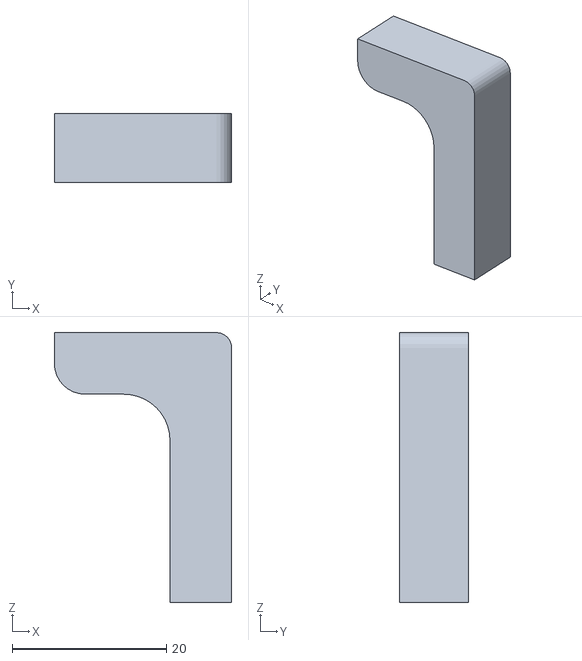
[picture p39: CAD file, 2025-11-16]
Components/angle.stl
23.0 x 9.00 x 35.0

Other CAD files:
Components/angle.ipt
Components/baza.ipt
Components/case.ipt
Components/karmashek.ipt
Components/moroshenka.ipt
Components/platform.ipt

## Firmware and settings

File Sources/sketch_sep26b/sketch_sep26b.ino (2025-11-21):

#include <SPI.h>
#include <MFRC522.h>
#include <SPIFFS.h> 

// #include "Data_Base.h"
#include "Terminal.h"
// #include "Key_Handler.h"

#define SS_PIN 5
#define RST_PIN 21
#define ANALOG_PIN 35

MFRC522 mfrc522(SS_PIN, RST_PIN);
MFRC522::StatusCode status;

Terminal terminal;
std::vector<uint8_t> received_UID;

void setup() {
  // Отключаем перезагрузку при открытии Serial
  Serial.setDebugOutput(false);
  delay(100);
  #ifdef ESP32
    Serial.setTxBufferSize(1024);
    Serial.setRxBufferSize(1024);
  #endif

  // Инициализируем файловую систему
  if (!SPIFFS.begin(true)) {
    Serial.println("Ошибка инициализации SPIFFS");
  }
  // Загружаем данные через terminal
  if (!terminal.load_data()) {
    Serial.println("Нет сохраненных данных");
  }
  if (!terminal.load_notes()) {
    Serial.println("Нет сохраненных заметок");
  }

  Serial.begin(9600); // Инициализация Serial-порта
  SPI.begin();          // Инициализация шины SPI

  mfrc522.PCD_Init();   // Инициализация RFID-модуля

  pinMode(ANALOG_PIN, INPUT);  // Настройка аналогового пина как вход

  mfrc522.PCD_SetAntennaGain(mfrc522.RxGain_max);  // Установка усиления антенны
  mfrc522.PCD_AntennaOff();           // Перезагружаем антенну
  mfrc522.PCD_AntennaOn();            // Включаем антенну

  delay(5000);
  Serial.print("\n");
  Serial.println("Inicialization saccess");
}

void loop() { 

  std::vector<std::string> cmd = terminal.read_command();
  if (cmd.size() > 0) {
      terminal.process_command(cmd);
  }
  delay(100);

  static uint32_t rebootTimer = millis(); // Важный костыль против зависания модуля!
  if (millis() - rebootTimer >= 1000) {   // Таймер с периодом 1000 мс
    rebootTimer = millis();               // Обновляем таймер
    digitalWrite(RST_PIN, HIGH);          // Сбрасываем модуль
    delayMicroseconds(2);                 // Ждем 2 мкс
    digitalWrite(RST_PIN, LOW);           // Отпускаем сброс
    mfrc522.PCD_Init();                   // Инициализируем заново
  }

  if (!mfrc522.PICC_IsNewCardPresent()) return; // Проверяем, поднесена ли новая метка. Если нет, выходим из loop и проверяем снова
  if (!mfrc522.PICC_ReadCardSerial()) return; // Пытаемся прочитать данные метки. Если не удалось, выходим из loop

  received_UID.clear();
  for (uint8_t  i = 0; i < mfrc522.uid.size; i++) {
    received_UID.push_back(mfrc522.uid.uidByte[i]);
  }


  terminal.buffer_UID(received_UID);
  
  // Останавливаем работу с меткой
  // mfrc522.PICC_HaltA();
  delay(1000);
}

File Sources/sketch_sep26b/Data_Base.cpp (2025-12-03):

#include <iterator>
#include <Arduino.h>
#include "Data_Base.h"
#include <Arduino_JSON.h>

std::string get_string(){
  std::string name = "";
  while (Serial.available() == 0) {
    delay(10);
  }
  while (true) {
    if (Serial.available() > 0) {
      char new_char = Serial.read();
      if (new_char == '\n' || new_char == '\r') {
        if (new_char == '\n') {
          break;
        }
      } else {
        name += new_char;
      }
      if (name.length() >= 128) {
        break;
      }
    }
    delay(1); // Небольшая задержка для стабильности
  }
  return name;
}

Data_Base::Data_Base(){
  Serial.print("Data_Base::Data_Base()\n");
}

Data_Base::~Data_Base(){
  for (auto it = person_data.begin(); it!=person_data.end(); it++){
    delete (it->second);
  }
  Serial.print("Data_Base::~Data_Base()\n");
}

bool operator==(const std::vector<uint8_t>& lhs, const std::vector<uint8_t>& rhs) {
    if (lhs.size() != rhs.size()) return false;
    for (int i = 0; i < lhs.size(); i++) {
        if (lhs[i] != rhs[i]) return false;
    }
    return true;
}

auto Data_Base::find_person(std::vector<uint8_t> person_UID){
  for (auto it = person_data.begin(); it!=person_data.end(); it++){
    if (it->first == person_UID){
      return it;
    }
  }
  return person_data.end();
}

auto Data_Base::find_person(std::string person_name){
  for (auto it = person_data.begin(); it!=person_data.end(); it++){
    if (it->second->get_name() == person_name){
      return it;
    }
  }
  return person_data.end();
}

auto Data_Base::find_person(int p_number){
  for (auto it = person_data.begin(); it!=person_data.end(); it++){
    if (it->second->get_person_number() == p_number){
      return it;
    }
  }
  return person_data.end();
}

Person* Data_Base::get_person(std::vector<uint8_t> person_UID){
  auto it = find_person(person_UID);
  return it->second;
}

auto Data_Base::get_map_end(){
  return person_data.end();
}

bool Data_Base::add_person(std::vector<uint8_t> person_UID){
  Serial.print("Trying to add person in Data_Base: ");
  for (int i =0; i< person_UID.size(); i++){
    Serial.print(person_UID[i]);
    Serial.print(' ');
  }
  Serial.print('\n');
  Person* person = new Person(person_UID);

  Serial.print("Enter the user`s full name\n");
  std::string p_name = get_string();
  person->rename(p_name);
  person_data[person_UID] = person;
  Serial.print("New person has been added\n");
  save_to_spiffs();
  return true;
}

bool Data_Base::add_person_json(std::vector<uint8_t> person_UID, std::string person_name){
  // load_from_spiffs();
  // Serial.print("Trying to add person in Data_Base: ");
  // for (int i =0; i< person_UID.size(); i++){
    // Serial.print(person_UID[i]);
    // Serial.print(' ');
  // }
  // Serial.print('\n');
  Person* person = new Person(person_UID);
  std::string p_name = person_name;
  person->rename(p_name);
  person_data[person_UID] = person;
  // Serial.print("New person has been added\n");
  // save_to_spiffs();
  return true;
}

bool Data_Base::delete_person(std::vector<uint8_t> person_UID){
  auto it = find_person(person_UID);
  if (it != person_data.end()){
    delete it->second;
    person_data.erase(it);
    save_to_spiffs();
    return true;
  }
  return false;
}

bool Data_Base::delete_person(int p_number){
  auto it = find_person(p_number);
  if (it != person_data.end()){
    delete it->second;
    person_data.erase(it);
    save_to_spiffs();
    return true;
  }
  return false;
}

bool Data_Base::take_key(std::vector<uint8_t> person_UID, int key_number){
  if (person_data.find(person_UID) == person_data.end()){ 
    Serial.print("This gay is noname\n");
    return false;
  }
  return person_data[person_UID]->take_key(key_number);
}
bool Data_Base::return_key(std::vector<uint8_t> person_UID, int key_number){
  if (person_data.find(person_UID) == person_data.end()){
    Serial.print("This gay is noname\n");
    return false;
  }
  return person_data[person_UID]->return_key(key_number);
}
bool Data_Base::give_access(std::vector<uint8_t> person_UID, int key_number){
  if (person_data.find(person_UID) == person_data.end()){ return false; }
  return person_data[person_UID]->add_key_access(key_number);
}
bool Data_Base::remove_access(std::vector<uint8_t> person_UID, int key_number){
  if (person_data.find(person_UID) == person_data.end()){ return false; }
  return person_data[person_UID]->remove_key_access(key_number);
}
int Data_Base::get_status(std::vector<uint8_t> person_UID, int key_number){
  if (person_data.find(person_UID) == person_data.end()){ return false; }
  return person_data[person_UID]->get_key_status(key_number);
}
bool Data_Base::give_access_by_number(int p_number, int key_number){
  if (find_person(p_number) == person_data.end()){ return false; }
  return find_person(p_number)->second->add_key_access(key_number);
}
bool Data_Base::remove_access_by_number(int p_number, int key_number){
  if (find_person(p_number) == person_data.end()){ return false; }
  return find_person(p_number)->second->remove_key_access(key_number);
}
bool Data_Base::check_door_access(std::vector<uint8_t> person_UID){
  if (find_person(person_UID) == person_data.end()){ return false; }
  return find_person(person_UID)->second->check_door_access();
}

void Data_Base::print_persons_data(){
  if (person_data.size() == 0){
    Serial.print("Data_Base is empty\n");
    return;
  }
  // int i = 1;
  for (auto it = person_data.begin(); it!=person_data.end(); it++){
    Serial.print(it->second->get_person_number());
    Serial.print(") ");
    it->second->print_info();
    // Serial.print("\n");
    // i++;
  }
}

// void Data_Base::print_persons_data(std::string p_name){
//   if (person_data.size() == 0){
//     Serial.print("Data_Base is empty\n");
//     return;
//   }
//   for (auto it = person_data.begin(); it!=person_data.end(); it++){
//     if (it->second->get_name() == p_name){ // точное совпадение
//       Serial.print(it->second->get_person_number());
//       Serial.print(") ");
//       it->second->print_info();
//     }
//     std::string = 
//   }
// }

void Data_Base::print_persons_data(std::string p_name){
  if (person_data.size() == 0){
    Serial.print("Data_Base is empty\n");
    return;
  }
  bool found = false;
  for (auto it = person_data.begin(); it != person_data.end(); it++){
    std::string person_name = it->second->get_name();
    // 1. Точное совпадение
    if (person_name == p_name) {
      Serial.print(it->second->get_person_number());
      Serial.print(") ");
      it->second->print_info();
      found = true;
      continue;
    }
    // 2. Простой поиск подстроки (фамилия/имя/отчество содержатся в ФИО)
    if (person_name.find(p_name) != std::string::npos) {
      Serial.print(it->second->get_person_number());
      Serial.print(") ");
      it->second->print_info();
      found = true;
    }
  }
  if (!found) {
    Serial.print("No persons found for: ");
    Serial.println(p_name.c_str());
  }
}
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

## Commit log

2025-09-16 Connect leds with arduino
    Гав
2025-10-18 prototype of case with sizes
    [case.ipt]
2025-10-20 first and maybe final product
    super puper
    [angle.ipt, moroshenka.ipt, platform.ipt]
2025-11-10 test json
    [Table.xlsx, data.csv, data.xlsx]
2025-11-13 Update README
    Доработка
2025-11-23 корпус для платы
    [baza.ipt]
2025-11-23 stl для печати
    [baza.stl]
2025-11-23 исправленная
    [moroshenka.stl]
2025-11-24 test circuit
2025-11-25 key_handler debugging
    [data.xlsx, esp32_persons_20251119_202114.xlsx, esp32_persons_20251125_231450.xlsx]
2025-11-29 data examples
    [data.xlsx, esp32_persons_20251125_231450.xlsx, esp32_persons_20251126_125929.xlsx]
2025-11-30 final code
    [esp32_notes_20251201_014754.xlsx]
2025-12-01 детальки по два вида каждой ( какая то одна точно влезет)
    [prot1.stl, prot2.stl, rectandirka.stl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]
